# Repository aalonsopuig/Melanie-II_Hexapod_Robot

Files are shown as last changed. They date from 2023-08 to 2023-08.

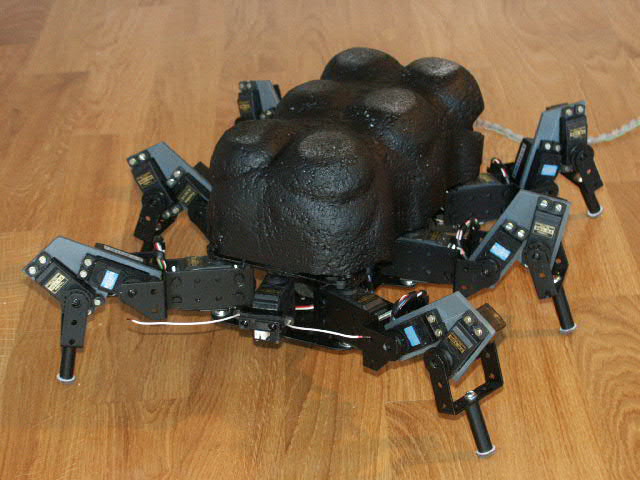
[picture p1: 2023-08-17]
Media/PICT0081.JPG

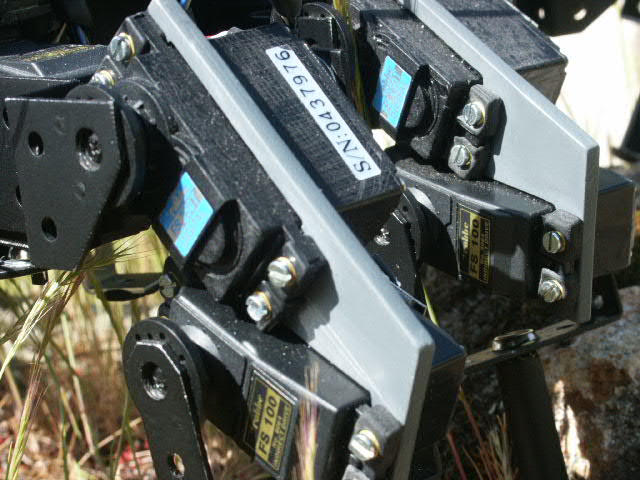
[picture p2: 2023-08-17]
Media/PICT0013.JPG

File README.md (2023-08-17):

<html>

<head>
<meta http-equiv="Content-Language" content="es">
<meta name="GENERATOR" content="Microsoft FrontPage 4.0">
<meta name="ProgId" content="FrontPage.Editor.Document">
</head>

<font size="4"><b><i>Melanie-II&nbsp;</i></b></font>
      <p>By Alejandro Alonso Puig<br>
      April 2004<br>
 
<hr>
<i>Melanie-II was developed by Alejandro Alonso on April 2004. This robot won the Hispabot 2004 National Robotics Contest at Spain.</i><br />
<i><br /></i>
<br />


<br />
Melanie is an hexapod robot of 3 degrees of freedom by leg, that by the novel design of legs it has, can transport several kilograms on its body without electrical power overload.&nbsp;The tests in laboratory have shown their capacity to rise and to walk at least with 4'5kg of additional charge, twice its own weight. See Video with <a href="https://youtu.be/sboOQ4rsUIg">Melanie-II carrying 4 bricks of milk</a><br />
<br />
<div>
<div style="text-align: center;">
<i><br /></i></div>
The version II that is showed in this technical report is an evolution of <b><u><a href="http://automacomp.blogspot.com.es/2004/03/melanie-v10-robust-hexapod-robot-of-3.html">Melanie-I</a></u></b>, to which some interesting capacities have been added, like the direct programming, the generation of movements by<br />
displacement of waves combined with inverse kinematics, or the capacity to walk on rough terrain. See Video with <a href="https://youtu.be/cWKl-8FBR9Y">Melanie-II walking over rough terrain</a><br />
<br />
There is a version III with superior capacities. Complete information could be obtained here: <b><u><a href="http://automacomp.blogspot.com.es/2004/09/melanie-iii-robust-hexapod-robot-of-3.html">Melanie-III</a></u></b><br />
<div>
<br /></div>
Some basic characteristics that define Melanie-II are the following:<br />
<br />
<i><u>Mechanics</u></i><br />
<ul>
<li>Size (cm): 33 x 31 x 20</li>
<li>Weight: 2.1 Kg</li>
<li>Structure of PVC and Aluminum</li>
<li>6 Legs. 3 degrees of freedom by leg.</li>
<li>Design of legs optimized to diminish consumption and to maximize power&nbsp;</li>
<li>Driven by radio control servos (Twelve of 3kgcm and six of 5kgcm)</li>
</ul>
<i><u>Electronics</u></i><br />
<ul>
<li>Servos control circuit with speed management, controlled via serial port.</li>
<li>I/O circuit, with 28 A/D conversion ports and 8 digital I/O. All chips are controlled via I2C bus. Measurement of the position of the 18 servos taking the signal of their potentiometers. Measurement of the consumption of energy of the servos by measuring the voltage drop in resistances of ½ ohm.&nbsp;</li>
<li>Battery of 6v NiMH 3300mAh for the servos</li>
<li>Battery of 9v NiCd for the control electronics</li>
<li>Distance measurement infrared sensor located at the front and able to be oriented</li>
</ul>
<i><u>Programming</u></i><br />
<ul>
<li>Control program in PC developed in Visual C++ 6.0</li>
<li>Movement sequence recording via direct programming</li>
<li>Movements generation by displacement of three simultaneous waves and use of inverse kinematics algorithms.</li>
<li>Detection of obstacles on the ground by detection of the variation in the current consumption and adaptation of the legs and trajectories to resolve it.</li>
</ul>
<br />
In this work there will be mention to all the mechanical, electronic and programming aspects, as well as conclusions of the experience.<br />
<br>
<br>
More information: <br>
<ul>
  <li><p align="justify"><a href="Documentation\melanie-II_doc_en.pdf">Technical documentation</a></li>
  <li><p align="justify"><a href="Melanie-II_Program">Program</a></li>
  <li><p align="justify"><a href="Media">Pictures</a></li>
  <li><p align="justify"><a href="https://github.com/aalonsopuig/Melanie-I_Hexapod_Robot.git">Repository of Melanie-I</a></li>
  <li><p align="justify"><a href="https://github.com/aalonsopuig/Melanie-III_Hexapod_Robot.git">Repository of Melanie-III</a></li>
</ul>

</body>

</html>

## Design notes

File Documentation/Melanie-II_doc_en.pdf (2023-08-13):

mundobot.com | Alejandro Alonso-Puig

# Melanie v2.0 Robust hexapod robot of 3 dof¹ /leg for rough terrain

Alejandro Alonso-Puig – mundobot.com April 2004

1
DOF: Degrees of Freedom

## Introduction

Melanie is an hexapod robot of 3 degrees of freedom by leg, that by the novel design of legs which it has, can transport several kilograms on its body without excessive power overload.

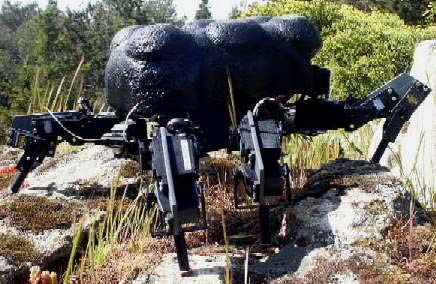
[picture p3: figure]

Some basic characteristics that define Melanie v2.0 are the following ones:

Mechanics

- Size (cm): 33 x 31 x 20
- Weight: 2.1 Kg
- Structure of PVC and Aluminum
- 6 Legs. 3 degrees of freedom by leg.
- Design of legs optimized to diminish consumption and to maximize power
- Driven by radio control servos (Twelve of 3kgcm and six of 5kgcm)

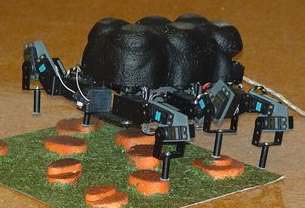
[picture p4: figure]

Electronics

- Servos | control | circuit | with | speed
management, controlled via serial port.
- I/O circuit, with 28 A/D conversion ports and 8 digital I/O. All chips are controlled via I² C
bus. Measurement of the position of the 18
servos | taking | the | signal | of their
potentiometers. | Measurement | of | the

consumption of energy of the servos by measuring the voltage drop in resistances of ½ ohm.
- Battery of 6v NiMH 3300mAh for the servos
- Battery of 9v NiCd for the control electronics
- Distance measurement infrared sensor located at the front and able to be oriented

Programming

- Control program in PC developed in Visual C++ 6.0
- Movement sequence recording via direct programming
- Movements generation by displacement of three simultaneous waves and use of inverse kinematics algorithms.
- Detection of obstacles on the ground by detection of the variation in the current consumption and adaptation of the legs and trajectories to resolve it.

In this work there will be mention to all the mechanical, electronic and programming aspects, as well as conclusions of the experience.

## Mechanics

Body

The trunk of Melanie is formed by a central chassis made out of two aluminum preperforated plates of 2mm, on which they are attached the six legs it has.

It has been procured the maximum symmetry possible in the body so that the center of gravity is the most centered possible and thus improves the physical behavior of the robot and distributes in a suitable way the effort throughout the legs.

The robot has been equipped with a shell of light porespan to protect the electronics and give it a more “animal” aspect.

Legs

The legs are made of aluminum of 2 mm and PVC of 4 mm. The structure of them differs from the habitual distribution of joints of the leg of an insect.

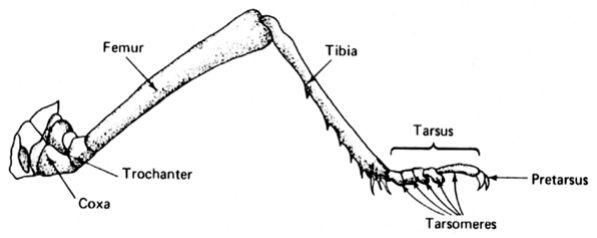
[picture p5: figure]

The Coxo-trochanter and trochanter-femur joints of an insect practically are fused, and they take care of the movements of femur in the space. The femur- tibia joint takes care of the movements of the tibia in the plane vertical to the ground.

The mechanical implementation of this structure usually is limited to three degrees of freedom and traditionally it implies the necessity to have an important torque in the servos due to the length of the femur. As longer it is, greater torque will be necessary in the motors. In addition, once carried out the elevation of the body, a great amount of energy is usually needed to maintain it in this position.

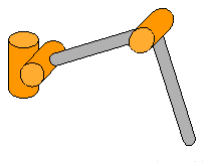
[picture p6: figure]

Traditional legs structure

The structure of legs of Melanie varies of the common structure shown in the above figure, modifying the position of the joints as it is shown the following figure:

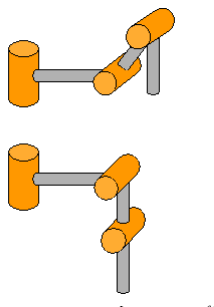
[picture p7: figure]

Legs structure of Melanie

With this structure two important advantages are obtained with respect to the traditional one shown previously:

1. Once elevated the body they are aligned the joints that allow the displacement in the vertical plane of the legs, which implies a drastic reduction of the energy consumption due to a reduction on the load in the motors of these joints. The final implementation has shown that in raised state the provision of energy to the motors can be cut and the robot will remain elevated, even with an additional charge (test with 1kg on its body). It is for that reason that will also be able to carry important additional charges in this position.
2. When moving the joint of the trochanter-femur zone to the femur-tibia zone, the mass center of the motors is moved towards the tibia, which releases of weight the trunk increasing the capacity to support a greater weight over it. The tests made have allowed verifying that each leg is able to elevate a weight of 800 grams in addition to the own weight of the leg. Reason why with 6 legs a trunk of 4,800 grams would be elevated. In the test bench the robot, of 2,1kg has risen with an additional charge of 4Kg.

The servo used are of 3Kgcm of torque for coxa and tibia joint and 5kgcm for the intermediate joint.

All the servos used have been mounted with false back shaft to assure a suitable attachment that avoids the torsions on the servo shaft.

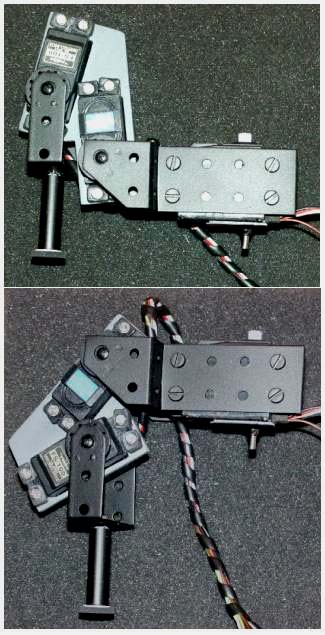
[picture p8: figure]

Leg structure of Melanie

## Electronics

Melanie v2.0 is based fundamentally on two cards: A commercial circuit of management of servos controlled by serial port RS232C of low cost and a I/O card with 28 A/D conversion ports and 8 digital ports.

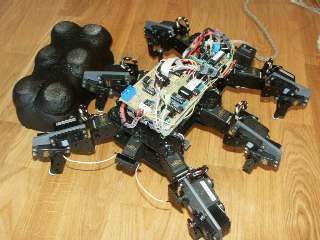
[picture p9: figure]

Servos control card

Card MSCC20 from Oricom Technologies (www.oricomtech.com) allows the control of up to 20 servos and in addition it allows to control the speed of each servo independently with just a single command.

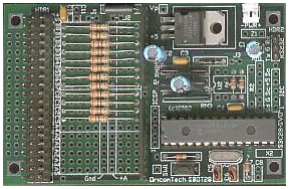
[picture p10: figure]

For additional information on this card it could be accessed its Internet web page, in which it will be found explanation of the usable Set of commands:
http://www.oricomtech.com/svo-cc.htm

The card is fed by a battery of 9v, being the servos fed by a battery of 6v NiMH 3.300 mAh

The card is connected via three wires cable to a PC serial port (RS232C) from which the control commands are sent.

I/O card

I/O Card is compound basically of 7 Chips PCF8591 (quadruple A/D of 8 bits controlled by I

2
C) and a chip PCF8574 (port expander of 8 bits by I²
C)

The 28 A/D channels are used for the measurement of the position of the 18 servos taking the signal from their potentiometers, for the measurement of the energy consumption of the 5Kgcm servos, measuring the fall of tension in resistance of ½ ohm and for the measurement of batteries voltage. As reference voltage it has been used 2,4v for the chips which measure the position of the servos and 1,4v for the chips which measure the consumption of the servos and the voltage of the batteries. For more details see the circuit diagram that is in the following figure.

Of the 8 digital channels only it is used one (channel 4). This channel activates the driver TC4425 that feeds a relay. This relay is used to cut the tension that goes to the 5Kgcm servos. This is used to reset servos since they are digital servos, that even maintain the position if we cut PWM signal. Causing a short fall of the tension in servo after stopping PWM signal they remain deactivated. Normal servos do not require this current cut as it is enough to stop the PWM signal in order to stop them. This deactivation is used for two aims: To deactivate by program the servos after a period of operation and to deactivate selectively servos to be able to move them manually and thus to make the direct programming.

Since I/O card is controlled by I²
C bus, it is used
an interface card between the robot and the external computer from which it is controlled. This card is the Velleman K8000. It is a commercial interface from parallel port to bus

I

2
C. Additional information could be obtained at: www.velleman.be or consulting the work of the author on the compatible KI²
C card of low cost in
http://www.mundobot.com/tecnica/ki2c/spki2c.htm

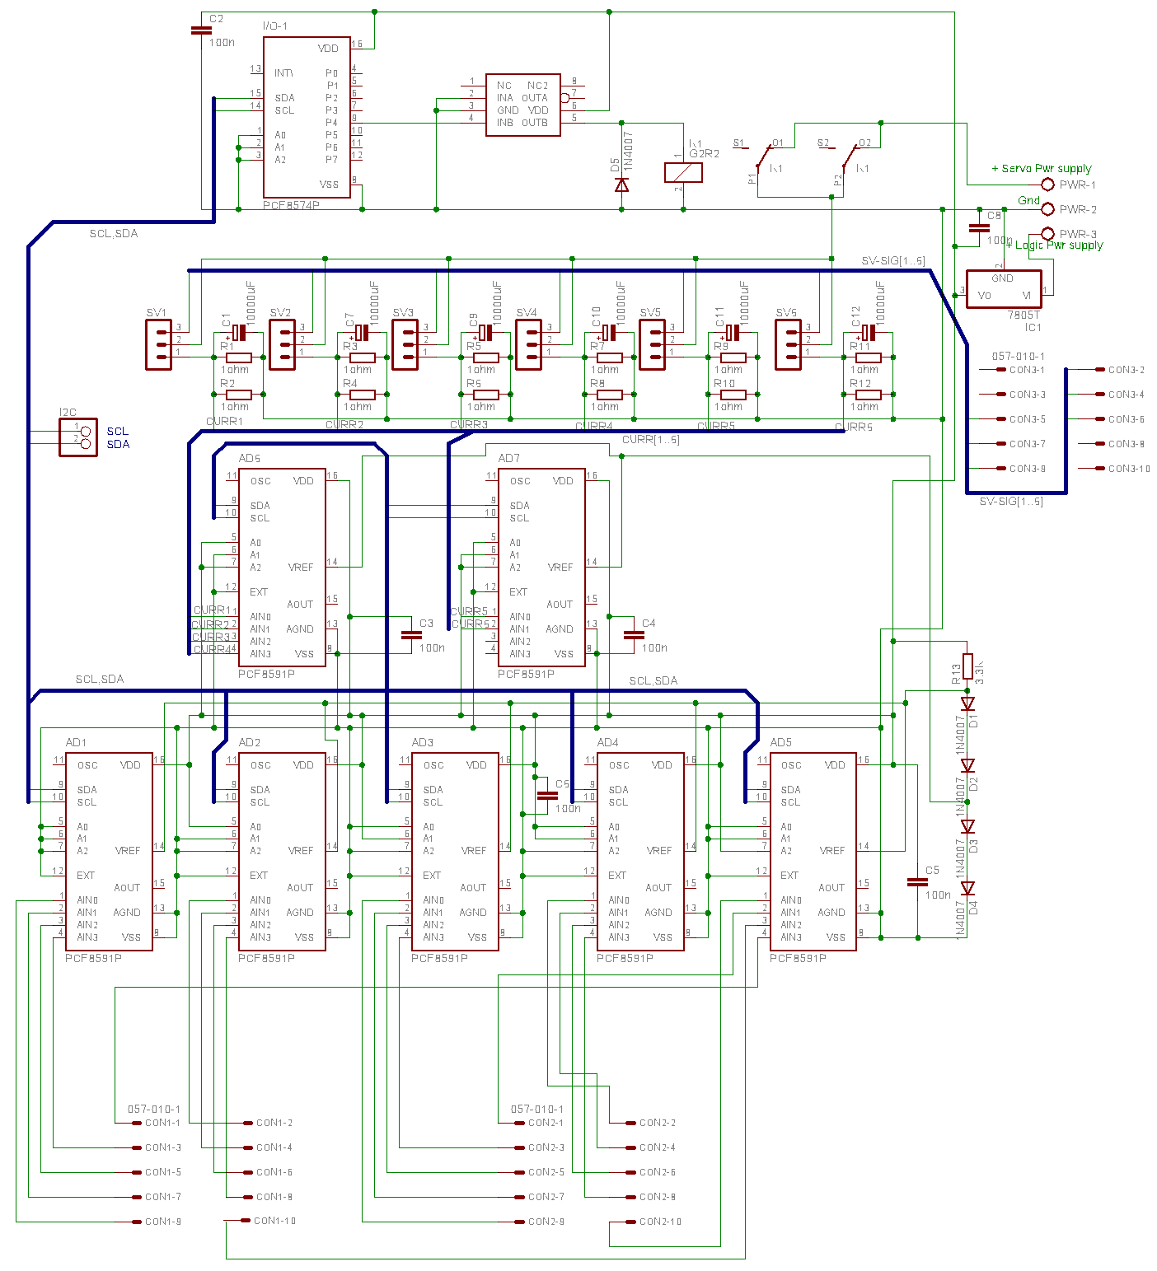
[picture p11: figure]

Following it is the relation of elements connected to connectors CON1, CON2 y CON3:

CON1-1 | Nothing | CON1-2 | Potentiometer Servo 12
CON1-3 | Potentiometer Servo 11 | CON1-4 | Potentiometer Servo 13
CON1-5 | Potentiometer Servo 6 | CON1-6 | Potentiometer Servo 5
CON1-7 | Potentiometer Servo 4 | CON1-8 | Potentiometer Servo 3
CON1-9 | Potentiometer
Servo 2 | CON1-10 | Potentiometer Servo 1
CON2-1 | Potentiometer Servo 14 | CON2-2 | Potentiometer Servo 15
CON2-3 | Potentiometer Servo 16 | CON2-4 | Potentiometer Servo 7
CON2-5 | Potentiometer Servo 8 | CON2-6 | Potentiometer Servo 9
CON2-7 | Potentiometer Servo 18 | CON2-8 | Potentiometer Servo 17
CON2-9 | Potentiometer Servo 19 | CON2-10 | Nothing

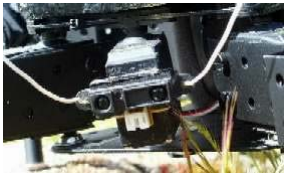
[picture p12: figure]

CON3-1 | Nothing | CON3-2 | PWM signal Servo 2
CON3-3 | Nothing | CON3-4 | PWM signal Servo 12
CON3-5 | PWM signal Servo 5 | CON3-6 | PWM signal Servo 15
CON3-7 | PWM signal Servo 8 | CON3-8 | Nothing
CON3-9 | PWM signal Servo 18 | CON3-10 | Nothing

On the other hand, to the connectors SV1,..SV6 they are connected the following digital servos (It would work the same with normal analogical servos):

SV1 | Servo 2 | SV2 | Servo 12
SV3 | Servo 15 | SV4 | Servo 18
SV5 | Servo 8 | SV6 | Servo 5

I

2
C addresses of the different chips are hardware set to the following decimal values:
AD1 | 144 | AD2 | 146
AD3 | 148 | AD4 | 150
AD5 | 152 | AD6 | 154
AD7 | 156 | I/O-1 | 64

Sensors

The robot has a GP2D12 infrared distance sensor in the frontal part, but in the present version it is not used.

## Software

For the control of the robot it has been developed the application "Melanie v2.0" in Visual C++ 6.0. This application is located in an external computer (Pentium II - 233Mhz, 64Mb ram, Windows 98). It sends the suitable commands to the servo control card of the robot via serial port and to the I/O control card by bus I²
C. This
control by bus I²
C is performed via the K8000 or KI²
C interface card connected to the parallel port that has been mentioned in the section of Electronics. The control of this card is carried out by specific libraries. For more details, see the work of the author in which its use is specified
widely: http://mundobot.com/tecnica/ecoi2c/specoi2c.htm

Use of the application

The interface with the user consists basically of the following dialogue box:

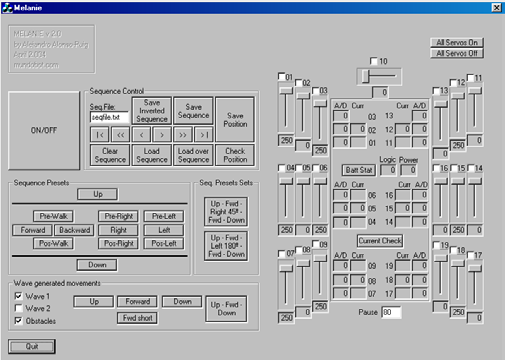
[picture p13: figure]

The dialogue box shows a series of controls that allow controlling the robot in a manual way and generating sequences of movements that can be recorded and later reproduced.

In order to activate the robot the button ON/OFF should be pressed, that will activate the legs maintaining them where they are.

Recording/Reproduction of sequences

The recording of sequences can be carried out by two ways:

- Moving the servos by means of sliding controls and recording the positions.
- Moving manually the legs and recording the positions by means of direct programming

Sliding controls

The right part shows the positioning values of the servos. Moving each slider control a servo will move.

A sequence could be recorded by positioning servos as desired so that the robot has a determined position, establishing a value of pause (field underneath the scheme of the robot), that will determine the time that should happen between the position that previously it had and the new one requested. Depending on this value, that will come measured in second hundredth, a greater or smaller speed will be applied to the servos.

Once selected position and pause, would press the button "Save Position" of the "Sequence Control" area, that will store the new position in dynamic memory. Following this way it is possible to generate a complete sequence of movements. Putting a name of file in the field "Seq.File" and pressing "Save Sequence" a file with the generated sequence will be recorded in hard disk.

Direct programming

In order to carry out this programming it would be necessary to deactivate the desired servos to be able to move them manually. This is carried out unmarking check-box of the wished servos in the right part of the screen. After this they could be moved manually to the wished position.

Once selected position and pause, we should press the button "Check Position", that will verify the position of legs servos and then "Save Position" of the area "Sequence Control", that will store the new position in dynamic memory. In this way we could store a complete sequence of movements. Putting a name of file in the field "Seq.File" and pressing "Save Sequence" a file with the generated sequence will be recorded in hard disk.

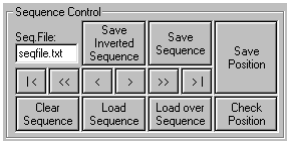
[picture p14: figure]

The other controls of the area "Sequence Control" carry out the following functions:

- Save Inverted Sequence: It records the sequence but in inverse way. Very useful when a movement is identical to another existing one but in the inverse way, like for example walking forwards and backwards
- Clear Sequence: Deletes the sequence that is in memory
- Load Sequence: Load in memory a prerecorded sequence. The name of the sequence file should be specified in the field "Seq.File"
- Load over Sequence: Load in memory a sequence from the present position of the pointer, that is to say, if we have a sequence in memory and we move to its end with the buttons we will explain later, we can press "Load Over Sequence" to load a sequence on the existing one in memory from the present position. This way we could connect sequences.
- "|<" Allows to be placed at the beginning of the existing sequence in memory
- ">|" Allows to be placed at the end of the sequence
- ">" Allows to advance a position in the sequence loaded in memory. This allows going step by step in the sequence for debugging.
- "<" inverse case of previous one
- ">>" Allows to reproduce the sequence from the present position to the end without interruption
- "<<" Just as the previous one but in inverse way.

With the previous controls it is possible to debug positions with advancing step by step, to correct the position wished with the slider controls and to press "Save Position".

It is necessary to consider that pressing this button overwrites the position of all servos in the present place of the sequence and the sequence pointer moves to the following position being prepared to overwrite it. If it is only wanted to overwrite a position, it will be done as indicated and then "<" and ">" should be clicked so the robot is forced to be placed according to the following position.

There is a series of prerecorded basic sequences that will allow moving the robot. These sequences are grouped under the set "Sequence Presets". They allow raising the robot, making it walk, turn...

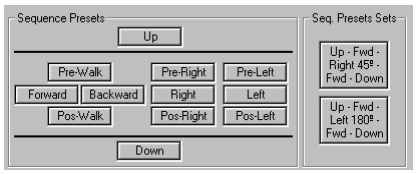
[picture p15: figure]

Additionally there is a group of sets of sequences prerecorded under the set "Sequence Preset Sets" that allow to execute several simple sequences of the indicated previously, to carry out a concrete task, demonstration, etc, like rising, walking, turning around and lying down.

Movements by displacement of waves over rough terrain

There is another area at the screen (wave generated movements) that allows controlling the robot not by playing recorded sequences, but by means of a system called waves displacement. The robot generate the movements based on triple overlapped waves.

The program is prepared for two kind of waves: Wave 1 and Wave 2. The first one makes the robot walk in the typical tripod mode, it means, walking with alternate triangles of legs so they are always three legs on the floor.

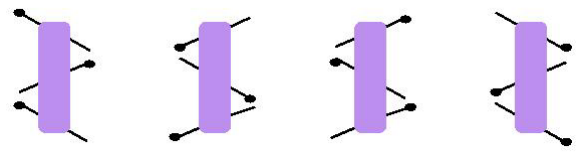
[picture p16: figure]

The second mode move the legs in a way so there are always five legs on the floor.

Also it is possible to make the robot sensible or not to obstacles on the floor by using the checkbox “Obstacles”. In case this mode is used, the robot will be able to walk in rough terrain, detecting obstacles like stones, walking over them while maintaining the body horizontal to the floor.

Application design

The application has been generated in Visual C++
6.0. It uses a library developed by P.J. Naughter for the control of the serial port with which the robot will communicate.

For more information on using the mentioned library the work of the existing author can be consulted in the direction:

http://www.codeproject.com/system/cserialport.asp

Additionally it uses a library for the control of the parallel-I²
C interface.

For more information on this library the following report could be reviewed:
http://mundobot.com/tecnica/ki2c/spki2c.htm

The interface with the user consists basically of a dialogue box associated to a CMelanieDlg class within which there are all the functions and variables used for the control of the robot.

The source code of the application contains numerous commentaries and can be acceded in the direction:
http://mundobot.com/projects/melanie/melanieprg.zip

In any case next we will explain the general structure of the application.

Recording/Reproduction of sequences

As it was explained previously, it is possible to store sequences of movements. In order to carry out this, pointers to structures stored in dynamic memory are used.

struct stPosition
{
unsigned char | cServoPos[21],
| cPause;
struct stPosition | *nextpos,
| *prevpos;
};

In each element of this structure we can store a complete position, that includes the 20 positions of servos and delay that must have between the previous position and this one. Additionally they are stored pointers both to previous and next elements to have a linked list in which we could move freely forward and backward.

The storage of the mentioned structure is performed when pressing the button “Save Position” which calls the function “OnSavepos()”. This function takes the servos position values and store them in the structure.

If direct programming is being performed, before pressing the button “Save Position” it is needed to press the button “Check Position” which will call the function “OnAD()” and this to “ChkPos(unsigned
char cPos[20],unsigned char cAD[20])” which takes the
servos position values by reading the analog values of the servos internal potentiometers. This value is converted to a byte value that if sent with the positioning command to the servo control card would move the servo to the position it is right now. To get this, the program have a table (byte bCal[21][4]) which stores four values for each servo that correspond to two different positions of the servos (a couple of values for each of the two positions). Each couple have interrelated values. The first one is the value sent to the servo control card to move the servo to that position. The second one is the analog measurement of the position. Having this for two different positions A and B (see figure), it is possible to obtain the rest of the values of the line that cross both points. Lets see this with an example:

Servo number 1 has been positioned with the slider controls to the value 20 (showed in the dialog box), then potentiometer value has been measured (A/D conversion). The value obtained has been 59. The same thing has been done locating the servo to position 198 obtaining the A/D value 195. As there is a linear relation between the positioning value and the A/D value,

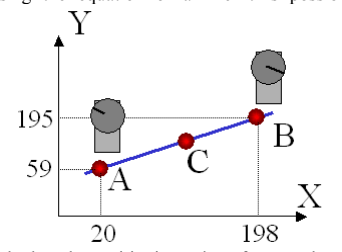
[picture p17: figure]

calculate the positioning value of a servo based on the A/D value measured. Then, if for example the value read from the potentiometer is, lets say 90, we will obtain the positioning value as showed here:

using the equation of a line it is possible to

osition = X axis

o points of the line = (20,59) y (198,195)

b = m(y-a) {Cartesian equation of a line}

sing the points: (x=20 , y=59, a=198, b=195)

-195= m(20 - 198)

= (59-195)/(20 - 198)

en :

-195 = m(x - 198) = (59-195)/(20-198)*(x-198)

D-195 = (59-195)/(20-198)*(POS-198)

OS = 198+(AD-195)/((59-195)/(20-198))

herefore, for AD=90, POS=60’6

has been taken therefore the values of A y B

he existing sequence in memory can be saved to

nly could be reproduced sequences that are

he execution of each step of the sequence is

P
AD = Y axis

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
empirically for all servos and charged them in the matrix bCal as part of the program code. In case of changing the servos, it would be necessary to calibrate them and to update the values of this matrix again.

T
a file using the function "OnSaveseq()"and load a
file | in | memory | using | the | function
"LoadSequence(CString FileName)" that is called from other several functions.

O
loaded in memory, so the buttons of prerecorded sequences simply will call to functions that load in memory a prerecorded sequence and executes it.

T
carried | out | by | calling | the | function
"SetGlobalPos()", that will move servo and slider controls according to the values of the present pointer.

The delay (Pause) as it was mentioned, will indicate the time that must pass between a position and another one. So that died moments do not exist, function " cSpeed(unsigned char cServo)" will calculate the speed that should apply to each servo depending on the mentioned pause and the run to carry out. It is based on specifications from the manufacturer of the servo control card that indicates that the speed parameter has to be an integer value between 1 and 255 that can be calculated according to the following formula:

T

Pos Pos V 8( | 1− | 0) =

where T is the time in second hundredth that is desired to take the servo to go from a position to another one, being Pos1 the position of greater value and Pos0 the position of lower value. The values of Pos1 and Pos0, according to specifications of the manufacturer of the servo control card, have to be integer values between 0 and 250.

The commands for the servo control card are
mainly | sent | by | using | the | function
"SendCommand(CString sCommand)".

Although the servo control card admits great amount of commands, we will use only the following ones:

- SO: It turn all servos on
- SF: turn all servos off
- SX1F9D: Set excursion limits of all servos to 496µsg and 2.512µsg
- SEss: It activates the generation of pulses for servo "ss", value that should be in hexadecimal 00 - 13h (19d).
- Mssddvv: It moves servo "ss" (hexadecimal value) to the 8 bits position "dd" (hexadecimal value between 00 and FAh [ 250d ]) at speed "vv" (hexadecimal value between 1 and FFh [ 255d ])

For more information on the commands available and their use, go to the documentation of the manufacturer:
http://www.oricomtech.com/sub2/msc2-cmd.htm

Movement by displacement of waves

As told before, the robot can move generating himself the positions instead of using prerecorded positions. The way in which it makes this is by using three waves whose values will vary in the time and will define the values of coordinates (x, y, z) in the space for the end of each leg.

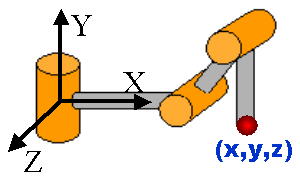
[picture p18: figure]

Having these values, a geometric algorithm of inverse kinematics will be used and the value of positioning of each servo will be obtained so that the end of the leg is placed in the indicated coordinates.

Inverse Kinematics

The program do all the inverse kinematics calculations needed by using the following function:

Int InvKinematic(double value[2][3], double result[3])

This function return 0 if it has not happened any error in the calculation (for example it could occur that the given coordinate is outside the reachable space of the leg).

The input data for the
function | will | be
loaded in the matrix
value[2][3] so that the
first row of data will
contain the lengths in

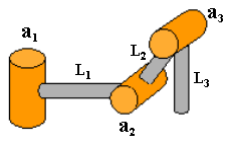
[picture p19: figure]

millimeters of the three parts of the leg (L1, L2, L3) and the second row will contain the coordinates (x, y, z) that is desired that it has the end of the leg respect to his origin of reference. As result the function loads in the matrix result[3] the values in degrees of the angles the joints should have (a1, a2, a3)

The algorithm used for the calculation of the inverse kinematics use the geometric method.

Later the values of angles (in degrees) of each servo can be converted to positioning values accepted by the servo control card by using the
function unsigned char cConvDegToPos(char cServo,
double Deg), where cServo is the number of the servo we are referring to and Deg is the value in degrees we desire this joint to have. The value returned by the function is the value to be sent to the servo control card.

In order to obtain this, values of calibration for each servo are used that have been taken empirically and are loaded at the beginning
of the program in matrix cPosConv[20][2].

The first index indicates the servo and the second index indicates a position of 0 degrees and one of 45 degrees. For example, for leg 1 the following values are loaded:

cPosConv[ 1][0]=203; | cPosConv[ 1][1]=140;
cPosConv[ 2][0]= 77; | cPosConv[ 2][1]=136;
cPosConv[ 3][0]=103; | cPosConv[ 3][1]=160;

The first row includes the values for servo 1. 203 is the value that requires the servo control card for positioning the servo so that the angle of the joint is 0 degrees and 140 is the value that requires the servo control card for positioning the servo so that the angle of the joint is 45 degrees.

With these values and, given to the linear relation between value of positioning and angle in degrees of the joint, we can always obtain the value of positioning of the servo based on the value of the angle of the joint by using the equation of a line.

It exists an inverse function to this called
double cConvPosToDeg(char cServo, unsigned char cPos)

Direct Kinematics

The program also carries out in some cases direct kinematics calculations. For it it uses the function:

int FwdKinematic (double value[2][3], double result[3])

This function returns 0 if it has not happened any error in the calculation.

The used algorithm is also of geometric type.

The input data for the
function | will | be
loaded in the matrix
value[2][3] so the first
row of data will
contain the lengths in

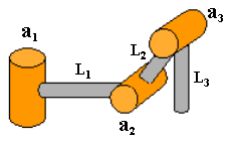
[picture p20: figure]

millimeters of the three parts of the leg (L1, L2, L3) and the second row will contain the angles in degrees of the joints (a1, a2, a3). As result the function will load in the matrix result[3] the values of the coordinates (x, y, z) that the end of the leg will have respect to its origin of reference.

Generation of waves

As told before, they are three waves those that define the coordinates that each leg will have at every moment.

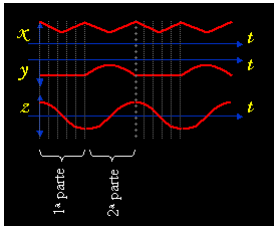
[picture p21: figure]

Coordinate X is calculated by means of a triangular wave, the coordinate Y by means of a half-wave and coordinate Z by means of a complete sine wave. The frequency of the triangular wave has to be double of the other two so that the leg moves suitably.

Varying the phase angle between the waves of the different legs and the relation between the length from the first (1ª Parte) and second part (2ª Parte)

of the cycle of the wave we will obtained different "gaits".

The first part of the cycle corresponds to the moment at which the end of the leg is touching the ground and moving backwards (body advancing), whereas the second part of the cycle corresponds to the elevation and displacement ahead in arc of the leg (positioning for a new step). Thus for example in the previous figure, the first and second part of the cycle is of the same length (in time), so it will take the same time in moving backwards the leg that in positioning it again ahead. If we used this type of waves
in all the legs, but we apply a phase angle of 180 degrees to three of the legs, we will obtain a tripod "gait", so the body always will be supported by three legs.

If for example we use waves of the previous type, but with the 2nd part of the cycle of a length 1/5 of the one of the 1st part the leg will rise and place ahead in a determined time, whereas it will move backwards 5 times slower.

If we combine this situation with a phase angle of 36º (180/5) between the waves of the different legs we obtain a "gait" according to which always there will be 5 legs on the ground and one in the air, but the body will be moving ahead with a continuous speed.

This is not accidental. If we wish that the body moves at continuous speed, it always has to have a sufficient number of legs in contact with the ground being moved backwards, not being anyone stopped. If we want that always there are 5 legs in contact with the ground, it will be necessary to raise the legs one by one, so that the 5 legs should have enough time to rise and be placed at the front in consecutive way in the time that the sixth leg moves backwards. So the time for the elevation and displacement of a leg in the air to the front will have to be 1/5 of the time that takes in moving the leg backwards. This is indeed the length in time of 2nd part of the cycle. On the other hand, as it is desired that only one leg is in the air at each moment (5 legs in the ground), the waves of the legs will have to be moved 1/5 of

180º, since 180º is the point in which the wave change from the 1st to the 2nd part of the cycle.

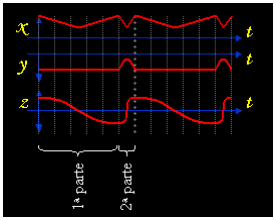
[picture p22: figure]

It is important in this point to stand out that the waves used are those indicated at the beginning of this section, so triangular, half-wave and complete sine wave and that the variation of the length in time of 1st or 2nd part of the cycle is just a kind of "stretching" of the time and therefore the values in degrees also "stretch". Lets see what we are talking about for the previous case of the sine wave (Cosenoidal) that generates the value of coordinate Z:

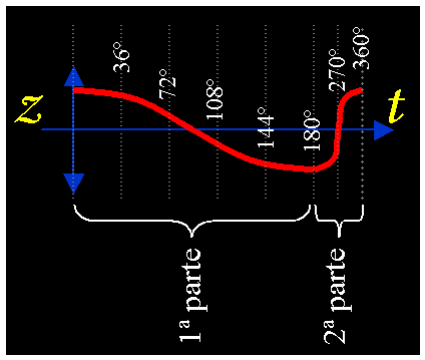
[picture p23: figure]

In the program it is the function void OnWaveFwd() that will make the robot walk forward according to the method of displacement of waves explained.

Following the same method of displacement of waves the MoveLeg function has been generated, that moves the end of one or several legs from a point in the space to another one, either with a straight line displacement between both points or making an arched movement of rise, displacement and go down.

It must be remembered that the coordinates handled for each leg are always relative to the point of coordinates of each leg, as showed in the following figure:

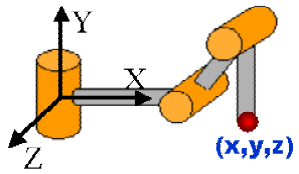
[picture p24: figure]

Obstacles detection

The program is prepared for the detection of obstacles on the ground and to adapt the "gait" to allow the robot to walk over these obstacles.

The way it is done is by measuring the consumption of current by the servos at the moment the leg is going down to put its end on the ground.

The measurement of the current consumption is done by the function void ChkCurr() that sends the needed commands to carry out the reading of A/D converters by bus I²
C and load in the
Current[6] matrix the values of measurement of current for the 6 servos that more force have to make to support the body.

If the consumption measurement is over a given threshold, the leg stops, its position is obtained and the length of the second part of the cycle of the waves of this leg is modified temporarily. Also a small phase angle is added to assure that they move with coordination with the rest of legs. The values of phase and length of the second part of the cycle of this leg return to its normal values in the following cycle, with no disruption in the continuity of the waves during the transition.

## Bibliography and interesting links

Agricultural Entomology. Daniel G. Pesante Armstrong. Chapter 7: http://www.uprm.edu/wciag/anscience/dpesante/4008/cap-7.PDF Puchobot. Quadruped Robot. Andrés Prieto Moreno: http://www.iearobotics.com/personal/andres/proyectos/pucho/pucho.html Cube Reloaded. Worm robot. Juan González: http://www.iearobotics.com/personal/juan/doctorado/cube-reloaded/
Direct & inverse kinematics course (Univ.Guadalajara-Mexico):: http://proton.ucting.udg.mx/materias/robotica/r166/r78/r78.htm
Legs. General design considerations: http://www.frasco.demon.co.uk/rodney/mechan/design.htm The Walking Machines Catalogue: http://www.walking-machines.org/
Silo4. Quadruped Robot developed by CSIC. Spain: http://www.iai.csic.es/users/silo4/
An introduction to robot kinematics: http://www.generalrobotics.org/ppp/Kinematics_final.ppt MSCC20. credit card-sized control computers for driving up to 20 R/C servos. Oricom Technologies: http://www.oricomtech.com/svo-cc.htm
CSerialPort v1.03 - Serial Port Wrapper. PJ Naugter: http://www.codeproject.com/system/cserialport.asp

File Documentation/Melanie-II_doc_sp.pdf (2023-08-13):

mundobot.com | Alejandro Alonso Puig

# Melanie v2.0 Robot hexápodo robusto de 3 dof¹ /pata para terrenos abruptos

Alejandro Alonso Puig – mundobot.com Abril 2004

1
DOF: Degrees of Freedom = Grados de Libertad

## Introducción

Melanie es un robot hexápodo de 3 grados de libertad por pata, que por el novedoso diseño de patas de que dispone, puede transportar varios kilos sobre su cuerpo sin excesiva sobrecarga energética.

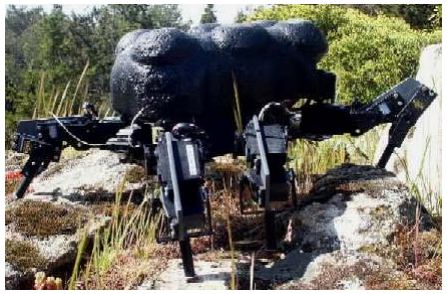
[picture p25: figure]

Algunas características básicas que definen a Melanie v 2.0 son las siguientes:

Mecánica

- Medidas (cm): 33 x 31 x 20
- Peso: 2.1 Kg
- Estructura de PVC y Aluminio
- 6 Patas. 3 grados de libertad por pata.
- Diseño de patas optimizado para minimizar consumo y maximizar potencia
- Accionamiento | mediante | servos | de
radiocontrol (Doce de 3kgcm y seis de 5kgcm)


Electrónica

- Circuito de control de servos con gestión de velocidad, controlado por puerto serie.
- Circuito I/O, con 28 puertos de conversión A/D y 8 entradas/salidas digitales. Todos los chips son controlados por bus I²
C. Medición
de la posición de los 18 servos tomando la señal de sus potenciómetros. Medición del consumo de energía de los servos midiendo la caída de tensión en resistencias de ½ ohm.
- Batería de 6v NiMH 3300mAh para la alimentación de los servos
- Batería de 9v NiCd para la alimentación de la electrónica de control
- Sensor de medición de distancia por infrarrojos delantero orientable

Programación

- Programa de control en PC desarrollado en Visual C++ 6.0
- Grabación de secuencias de movimiento por programación gestual
- Generación | de | movimientos | por
desplazamiento de tres ondas simultáneas y aplicación de algoritmos de cinemática inversa
- Detección de obstáculos en el suelo por variación en el consumo de corriente y adaptación de las patas y trayectorias para solventar los mismos.

En este trabajo se hará mención a todos los
aspectos | mecánicos, | electrónicos | y | de
programación, así como conclusiones de la experiencia.

## Mecánica

Cuerpo

El tronco de Melanie está formado por un chasis central consistente en dos planchas de aluminio preperforado de 2mm sobre el que se acoplan las seis patas de que dispone.

Se ha procurado la máxima simetría posible en el cuerpo para que el centro de gravedad quede lo más centrado posible en el mismo y así mejorar el comportamiento físico del robot y distribuir de forma adecuada el esfuerzo de las patas.

Se ha dotado al robot de un caparazón de porespan ligero para proteger la electrónica y dotarle de una imagen más “animal”.

Patas

Las patas se han construido en aluminio de 2 mm y PVC de 4 mm. La estructura de las mismas difiere de la distribución de articulaciones habitual de la pata de un insecto.


Las articulaciones Coxo-trocanter y trocanter-fémur de un insecto se encuentran prácticamente fundidas entre si y se ocupan de los movimientos del fémur en el espacio. La articulación fémur-tibia se ocupa de los movimientos de la tibia en el plano vertical al suelo.

La implementación mecánica de esta estructura suele limitarse a tres grados de libertad y tradicionalmente implica la necesidad de disponer de un par motor importante en los servos debido a la longitud del fémur. Cuanto más largo sea este, mayor par será necesario en los motores. Además, una vez efectuado el elevamiento del cuerpo, es necesaria una cuantiosa cantidad de energía para mantenerlo en dicha posición.

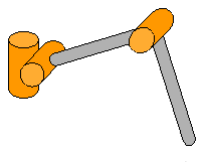
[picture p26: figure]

Estructura tradicional de patas

La estructura de patas de Melanie varía de la estructura común mostrada en la figura de arriba, modificando la posición de las articulaciones tal como se muestra en la figura siguiente:


Estructura de patas de Melanie

Con esta estructura se obtienen dos ventajas importantes respecto a la tradicional mostrada previamente:

1. Una vez levantado el cuerpo se superponen las articulaciones que permiten el desplazamiento en el plano vertical de las patas, lo que implica una drástica reducción del consumo de energía al reducir la carga en los motores de dichas articulaciones. La implementación final ha demostrado que en estado levantado puede cortarse el suministro de energía a los motores y el robot permanecerá elevado, incluso con carga adicional (test con 1kg sobre su cuerpo). Es por ello que podrá además llevar cargas adicionales importantes en esta postura.
2. Al desplazar la articulación de la zona del trocanter-fémur a la zona fémur-tibia se desplaza el peso de los motores hacia la tibia, lo que libera de peso al tronco aumentando la capacidad de soportar un peso mayor sobre el mismo. Los ensayos realizados sobre banco de pruebas han permitido comprobar que cada pata es capaz de elevar un peso de 800 gramos además del propio peso de la pata. Por lo que con 6 patas podría elevarse un tronco de 4.800 gramos. En el banco de pruebas el robot, de 2,1kg se ha levantado con una carga adicional de 4Kg.

Los servos utilizados son de 3Kgcm de par para coxa y articulación de la tibia y 5kgcm para la articulación intermedia.

Todos los servos utilizados han sido montados con falso eje posterior para asegurar un adecuado anclaje que evite las torsiones sobre el eje de los mismos.


Estructura de patas de Melanie

## Electrónica

Melanie v2.0 se basa fundamentalmente en dos tarjetas: Un circuito comercial de gestión de servos controlado por puerto serie RS232C de bajo coste y una tarjeta I/O con 28 puertos de conversión A/D y 8 entradas/salidas digitales.


Tarjeta de gestión de servos

La tarjeta MSCC20 de Oricom Technologies (www.oricomtech.com) permite el control de hasta 20 servos y además permite controlar la velocidad de cada servo de forma independiente con un solo comando.


Para información adicional sobre dicha tarjeta puede accederse a la página sobre la misma en

Internet, en la cual se puede encontrar explicación del set de comandos utilizable: http://www.oricomtech.com/mscc20.htm

La tarjeta está alimentada por una batería de 9v, estando los servos alimentados por una batería de 6v NiMH de 3.300 mAh

La tarjeta está conectada mediante un cable de tres hilos al puerto serie de un PC desde el que se envían los comandos de control.

Tarjeta I/O

La tarjeta I/O está compuesta básicamente por 7 chips PCF8591 (cuádruple A/D de 8 bits controlados por I²
C) y un chip PCF8574 (expansor de puerto de 8 bits por I²
C)

Los 28 canales A/D son utilizados para la medición de la posición de los 18 servos tomando la señal de sus potenciómetros, para la medición del consumo de energía de los servos de 5Kgcm de par, midiendo la caída de tensión en resistencias de ½ ohm y para la medición de tensión de las baterías. Como voltaje de referencia se ha utilizado 2,4v para los chips que miden la posición de los servos y 1,4v para los chips que miden el consumo de los servos y la tensión de las baterías. Para más detalles ver el plano del circuito que se muestra en la siguiente figura.

De los 8 canales digitales solo se utiliza uno de ellos como salida (canal 4). Dicho canal da señal a un driver de potencia TC4425 que alimenta un Relé. Este Relé se utiliza para cortar la tensión que va a los servos de 5Kgcm de par. Esto se utiliza para resetear dichos servos ya que son servos digitales, que mantienen la posición incluso si se corta la señal PWM de posicionamiento. Provocando una caída corta de la tensión en dichos servos tras cortar la señal PWM se quedan desactivados. Los servos normales no requieren este corte de corriente ya que al cortar la señal PWM quedan inmediatamente desactivados. Esta desactivación se utiliza para dos fines: Desactivar por programa los servos tras un periodo de funcionamiento y desactivar selectivamente servos para poder moverlos manualmente y así realizar la programación gestual.

Puesto que la tarjeta I/O está controlada por bus I

2
C, se utiliza una tarjeta interface entre el robot y el ordenador externo desde el que se controla el mismo. Esta tarjeta es la Velleman K8000. Se trata de un interfaz comercial de puerto paralelo a bus I

2
C. Se puede obtener información adicional en la página www.velleman.be o consultando el trabajo del autor sobre la tarjeta compatible de bajo coste KI²
C en http://www.mundobot.com/tecnica/ki2c/spki2c.htm


A continuación se muestra la relación de elementos conectados a los conectores CON1, CON2 y CON3:

CON1-1 | Nada | CON1-2 | Potenciómetro Servo 12
CON1-3 | Potenciómetro Servo 11 | CON1-4 | Potenciómetro Servo 13
CON1-5 | Potenciómetro Servo 6 | CON1-6 | Potenciómetro Servo 5
CON1-7 | Potenciómetro Servo 4 | CON1-8 | Potenciómetro Servo 3
CON1-9 | Potenciómetro
Servo 2 | CON1-10 | Potenciómetro Servo 1
CON2-1 | Potenciómetro
Servo 14 | CON2-2 | Potenciómetro Servo 15
CON2-3 | Potenciómetro Servo 16 | CON2-4 | Potenciómetro Servo 7
CON2-5 | Potenciómetro Servo 8 | CON2-6 | Potenciómetro Servo 9
CON2-7 | Potenciómetro Servo 18 | CON2-8 | Potenciómetro Servo 17
CON2-9 | Potenciómetro Servo 19 | CON2-10 | Nada
CON3-1 | Nada | CON3-2 | Señal PWM Servo 2
CON3-3 | Nada | CON3-4 | Señal PWM Servo 12
CON3-5 | Señal PWM Servo 5 | CON3-6 | Señal PWM Servo 15
CON3-7 | Señal PWM Servo 8 | CON3-8 | Nada
CON3-9 | Señal PWM Servo 18 | CON3-10 | Nada


Por otra parte, a los conectores SV1,..SV6 se conectan los siguientes servos, que son de tipo digital (funcionaría igual con servos analógicos normales):

SV1 | Servo 2 | SV2 | Servo 12
SV3 | Servo 15 | SV4 | Servo 18
SV5 | Servo 8 | SV6 | Servo 5

Las direcciones I²
C de los diferentes chips se han establecido por hardware a los siguientes valores:
AD1 | 144 | AD2 | 146
AD3 | 148 | AD4 | 150
AD5 | 152 | AD6 | 154
AD7 | 156 | I/O-1 | 64

Sensores

El robot posee un sensor de distancia por infrarrojos GP2D12 en la parte frontal, pero en la versión actual no es utilizado.

## Programación

Para el control del robot se ha generado la aplicación “Melanie v2.0” en Visual C++ 6.0. Dicha aplicación se encuentra localizada en un ordenador externo al robot (Pentium II – 233Mhz, 64Mb RAM, Windows 98). Se ocupa de enviar los comandos adecuados a la tarjeta de control de servos del robot vía puerto serie y controlar la tarjeta I/O por bus I²

C. Dicho control por bus I² C
se hace a través de la tarjeta interface K8000 o KI²
C conectada al puerto paralelo que se ha mencionado en el apartado de Electrónica. El control de esta tarjeta se lleva a cabo mediante el uso de unas librerías específicas. Para más
detalles | ver | el | trabajo | del | autor:
http://mundobot.com/tecnica/ecoi2c/specoi2c.htm en el que se especifica ampliamente su uso.

Utilización de la aplicación

El interface con el usuario consiste básicamente en un cuadro de diálogo como el que se muestra a continuación.


El cuadro de diálogo muestra una serie de controles que permiten manejar al robot de forma manual y generar secuencias de movimientos que
pueden | ser | grabadas | y | posteriormente
reproducidas.

Para activar el robot habrá de pulsarse en primer lugar el botón ON/OFF, que activará las patas dejándolas fijas en la posición actual.

Grabación/Reproducción de
secuencias

La grabación de secuencias puede llevarse a cabo de dos formas:

- Moviendo los servos mediante controles deslizantes y grabando las posiciones
- Moviendo manualmente las patas y grabando las posiciones mediante programación gestual

Controles deslizantes

La parte derecha muestra los valores de posicionamiento de los servos. Moviendo cada control deslizante se moverá un servo concreto.

Pueden grabarse secuencias posicionando los servos como se desee para que el robot tenga una postura determinada, estableciendo un valor de pausa (campo debajo del esquema del robot), que determinará el tiempo que habrá de pasar entre la postura que anteriormente tuviese y la nueva fijada. Dependiendo de dicho valor, que vendrá medido en centésimas de segundo, se aplicará una mayor o menor velocidad a los servos.

Una vez seleccionada postura y pausa, se pulsaría el botón “Save Position” del área “Sequence Control”, que almacenará la nueva posición en memoria dinámica. Se puede de esta manera ir guardando nuevas posiciones generando una secuencia completa de movimientos. Poniendo un nombre de fichero en el campo “Seq.File” y pulsando “Save Sequence” se grabará en disco duro un fichero con la secuencia generada.

Programación gestual

Para llevar a cabo esta programación habría que desactivar los servos que se desee para poder moverlos manualmente. Esto se lleva a cabo desmarcando los check-box de los servos deseados en la parte derecha de la pantalla. Tras esto pueden moverse manualmente hasta la posición deseada.

Una vez seleccionada postura y pausa, se pulsaría el botón “Check Position”, que verificará la posición de los servos de las patas y luego “Save Position” del área “Sequence Control”, que almacenará la nueva posición en memoria dinámica. Se puede de esta manera ir guardando nuevas posiciones generando una secuencia completa de movimientos. Poniendo un nombre de fichero en el campo “Seq.File” y pulsando “Save Sequence” se grabará en disco duro un fichero con la secuencia generada.


Los demás controles del área “Sequence Control” llevan a cabo las siguientes funciones:

- Save Inverted Sequence: Graba la secuencia pero en sentido inverso. Muy útil cuando un movimiento es idéntico a otro existente pero a la inversa, como por ejemplo andar hacia delante y hacia atrás.
- Clear Sequence: Borra la secuencia que hubiese en memoria.
- Load Sequence: Carga en memoria una secuencia pregrabada. Ha de especificarse el nombre de la misma en el campo “Seq.File”
- Load over Sequence: Carga en memoria una secuencia desde la posición actual de memoria, es decir, si tenemos una secuencia en memoria y nos colocamos al final de la misma con los botones que se explicarán a continuación, podemos pulsar “Load Over Sequence” para cargar una secuencia sobre la existente desde la posición actual. De esta manera se pueden enlazar secuencias.
- “|<” Permite colocarse al principio de la secuencia existente en memoria
- “>|” Permite colocarse al final de la secuencia.
- “>” Permite avanzar una posición en la secuencia cargada en memoria. Esto permite ir paso a paso en la secuencia para depurarla.
- “<” Caso inverso del anterior.
- “>>” Permite reproducir la secuencia desde el punto actual hasta el final sin interrupción.
- “<<” Igual que el anterior pero de forma inversa.

Con los controles anteriores es posible depurar posiciones a base de avanzar paso a paso, corregir la posición deseada con los controles deslizantes y pulsar “Save Position”.

Hay que tener en cuenta que al pulsar este botón se sobrescribe la postura de todos los servos en el lugar actual de la secuencia y el puntero de secuencia se mueve a la siguiente posición quedando preparado para sobrescribirla. Si tan solo se quiere sobrescribir una posición, se hará como se ha indicado y luego se pulsará “<” y luego “>” con lo que forzamos al robot a colocarse según la posición siguiente.

Hay una serie de secuencias básicas pregrabadas que permitirán mover el robot. Dichas secuencias se encuentran agrupadas bajo el conjunto “Sequence Presets”. Permiten levantar el robot, prepararlo para andar, girar,...


Adicionalmente hay un grupo de sets de secuencias pregrabadas bajo el conjunto “Sequence Preset Sets” que permiten ejecutar varias secuencias simples de las indicadas anteriormente para llevar a cabo una tarea concreta, demostración, etc, como levantarse, dar unos pasos, dar la vuelta y volver a tumbarse.

Movimiento por desplazamiento de ondas sobre terreno abrupto

Existe otro área en la pantalla (wave generated movements) que permite controlar el robot no mediante la reproducción de secuencias
pregrabadas, | sino | mediante | un | sistema
denominado de desplazamiento de ondas. El propio robot genera los movimientos basados en triples ondas superpuestas.

El programa está preparado para dos tipos de ondas: Wave 1 y Wave 2. La primera hace que el robot ande en modo trípode, es decir, alternando un triángulo de patas, de manera que siempre hay tres patas en el suelo. El segundo modo alterna los movimientos de las patas de manera que siempre estén 5 patas en el suelo.

Adicionalmente se puede hacer que el robot sea o no sensible a obstáculos en el suelo, marcando o no el checkbox “Obstacles”. En caso de marcarlo, el robot podrá detectar terreno abrupto, como por ejemplo piedras y caminar sobre ellas manteniendo el cuerpo horizontal al suelo.

Diseño de la aplicación

La aplicación se ha generado en Visual C++ 6.0. Utiliza una librería desarrolladas por P.J. Naughter para el control del puerto serie con el que se comunicará con el robot.

Para más información sobre el manejo de la mencionada librería puede consultarse el trabajo del autor existente en la dirección:
http://www.codeproject.com/system/cserialport.asp

Adicionalmente utiliza una librería para el control del interface paralelo-I

2
C

Para más información sobre el manejo de esta librería puede consultarse el trabajo del autor existente en la dirección:
http://mundobot.com/tecnica/ki2c/spki2c.htm

El interface con el usuario consiste básicamente en un cuadro de diálogo asociado a una clase CMelanieDlg dentro de la cual se encuentran todas las funciones y variables utilizadas para el control del robot.

Los ficheros fuente de la aplicación contienen numerosos comentarios explicativos y pueden ser accedidos en la dirección:
http://mundobot.com/projects/melanie/v2/melanie2prg.zip

No obstante a continuación explicaremos la estructura general de la aplicación.

Grabación/Reproducción de
secuencias

Como se explicó anteriormente, es posible almacenar secuencias de movimientos. Para llevar a cabo esto se utilizarán punteros a estructuras almacenadas en memoria dinámica.

struct stPosition
{
unsigned char | cServoPos[21],
| cPause;
struct stPosition | *nextpos,
| *prevpos;
};

En cada elemento de esta estructura podemos almacenar una postura completa, que comprende la posición de 20 servos y el delay que deberá haber entre la postura anterior y esta. Adicionalmente se almacenan punteros a los elementos anteriores y posteriores para tener una lista enlazada en la que nos podamos mover libremente hace delante y detrás.

El almacenamiento en dicha estructura se realiza al pulsar el botón “Save Position” que llama a la función “OnSavepos()”. Dicha función toma los valores de posición de servos existentes en el cuadro de diálogo y los almacena en la estructura.

Si se está haciendo programación gestual, antes de pulsar el botón “Save Position” habrá que pulsar el botón “Check Position” que llamará a la función “OnAD()” y esta a “ChkPos(unsigned char
cPos[20],unsigned char cAD[20])” que toma los
valores de posición de los servos a base de leer el valor analógico de posición de sus potenciómetros internos. Este valor es convertido al valor de tamaño byte que enviado con el comando de posicionamiento de la tarjeta de control de servos colocaría los servos en la misma posición en la que están. Para conseguir esto el programa posee una tabla (byte bCal[21][4]) que almacena para cada servo dos valores para dos puntos de posicionamiento de los servos. Uno de los valores es el que enviado a la tarjeta de control de servos para que posicione el servo y el otro valor es la medición analógica tomada en dicha posición. Teniendo esto para dos posiciones de un servo se pueden obtener los valores de todos los puntos intermedios. Veamos esto con un ejemplo:

Para el servo número 1 se posicionó con los controles deslizantes en el valor 20 (el mostrado en el cuadro de diálogo) y se tomó el valor del potenciómetro (conversión A/D). El valor obtenido fue 59. La misma operación se realizó colocando el servo en la posición 198 obteniendo el valor A/D 195. Puesto que hay una relación lineal entre un valor de posicionamiento y la


una recta se puede calcular, en función de un valor A/D dado, cual es el valor de posicionamiento del servo. Así, si por ejemplo se lee el valor A/D del servo (voltaje en la patilla central del potenciómetro del servo) y dicho valor es, digamos 90, tendremos que el valor de posicionamiento del servo se obtendrá de la

Posicion = eje X

medida A/D tomada, utilizando la ecuación de

siguiente forma:

D = eje Y

e la recta = (20,59) y (198,195)

8)

8) = (59-195)/(20-198)*(x-198)

o los valores de A y B
mpíricamente para todos los servos y se cargan

a puede ser
olcada a fichero mediante la función

secuencias que estén
argadas en memoria, por lo que los botones de

o de la secuencia se lleva cabo mediante la utilización de la función

A

dos puntos d

x-b = m(y-a) {ecuación cartesiana de una recta}

Usando los puntos: (x=20 , y=59, a=198, b=195)

59-195= m(20 - 198)

m = (59-195)/(20 - 19

entonces :

y-195 = m(x - 19

AD-195 = (59-195)/(20-198)*(POS-198)

POS = 198+(AD-195)/((59-195)/(20-198))

Para AD=90, POS=60,6

Se han tomado por tant
e
en la matriz bCal por programa. Si se cambiasen los servos habría que calibrarlos de nuevo y actualizar los valores de esta matriz.

La secuencia existente en memori
v
“OnSaveseq()”. De igual manera cargarse un fichero en memoria mediante la función “LoadSequence(CString FileName)” que es llamada desde otras varias.

Solo se pueden reproducir
c
secuencias pregrabadas simplemente llamarán a funciones que carguen en memoria una secuencia pregrabada y la ejecute.

La ejecución de cada pas
a
“SetGlobalPos()”, que moverá los servos y controles deslizantes según los valores del puntero actual.

El delay (Pause) como se ha dicho, indicará el tiempo que debe transcurrir entre una postura y otro. Para que no existan momentos muertos, la
función | “cSpeed(unsigned | char | cServo)”
calculará la velocidad que se ha de aplicar a cada servo dependiendo de la pausa mencionada y del recorrido a llevar a cabo. Para ello se basa en especificaciones del fabricante de la tarjeta de control de servos que indica que el parámetro de velocidad ha de ser un valor entero entre 1 y 255 que se puede calcular según la siguiente fórmula:
| T
Pos Pos V 8( | 1− | 0) =

onde T es el tiempo en centésimas de segundo

l envío de comandos a la tarjeta de control de

unque la tarjeta de control de servos admite gran

SO: Activa todos los servos

ites de duty cycle

- para el
- vo “ss” (valor

ara más información sobre los comandos

2/msc2-cmd.htm

d
que se desea que tarde el servo en ir de una posición a otra, siendo Pos1 la posición de valor mayor y Pos0 la posición de menor valor. Los valores de Pos1 y Pos0 según especificaciones del fabricante de la tarjeta de control de servos han de ser valores enteros entre 0 y 250.

E
servos se realiza fundamentalmente mediante la función “SendCommand(CString sCommand)”.

A
cantidad de comandos, nosotros utilizaremos solo los siguientes:
- SF: Apaga todos los servos
- SX1F9D: Establece los lím
de los servos entre 496µsg y 2512µsg
SEss: activa la generación de pulsos
servo “ss”, valor que ha de estar en hexadecimal 00 - 13h (19d).
Mssddvv: Mueve el ser
hexadecimal) a la posición de 8 bits “dd” (valor hexadecimal entre 00 y FAh [250d]) a la velocidad “vv” (valor hexadecimal entre 1 y FFh [255d])

P
disponibles y su utilización, acceder a la documentación del fabricante: http://www.oricomtech.com/sub

Movimiento por desplazamiento de ondas

Como se ha comentado anteriormente, el robot puede desplazarse generando él mismo las posiciones en lugar de utilizar posiciones pregrabadas. El modo en que realiza esto es mediante la utilización de tres ondas cuyos valores variarán en el tiempo y definirán los valores de coordenadas (x, y, z) en el espacio del extremo de cada pata.


Teniendo estos valores, se utilizará un algoritmo geométrico de cinemática inversa y se obtendrá el valor de posicionamiento de cada servo para que el extremo de la pata se coloque en las coordenadas indicadas.

Cinemática Inversa

El programa hace los cálculos cinemáticos inversos que sean necesarios mediante la función

Int InvKinematic(double value[2][3], double result[3])

Esta función devuelve 0 si no ha ocurrido ningún error en el cálculo (por ejemplo podría darse que la coordenada dada esté fuera del espacio alcanzable por la pata).

Los datos de entrada
de la función se
cargarán en la matriz
value[2][3] de manera
que la primera fila de
datos contendrá las


longitudes en milímetros de las tres partes de la pata (L1, L2, L3) y la segunda fila contendrá las coordenadas (x, y, z) que se desea que tenga el extremo de la pata respecto de su origen de referencia. Como resultado la función cargará en la matriz result[3] los valores en grados de los ángulos que han de tener las articulaciones (a1, a2, a3)

El algoritmo utilizado para el cálculo de la cinemática inversa es de tipo geométrico.

Posteriormente pueden convertirse los valores de ángulos en grados de cada servo a valores de posicionamiento aceptados por la tarjeta de control de servos mediante el uso de la función
unsigned char cConvDegToPos(char cServo, double Deg),
donde cServo es el número del servo al que nos referimos y Deg es el valor en grados que deseamos que tenga dicha articulación. El valor devuelto por la función es el valor a enviar a la tarjeta de control de servos.

Para conseguir esto se utilizan valores de calibración para cada servo que han sido tomados empíricamente y son cargados al principio del programa en la matriz cPosConv[20][2].

El primer índice indica el servo y el segundo índice indica una posición de 0 grados y una de 45 grados. Por ejemplo, para la pata 1 se cargan los siguientes valores:

cPosConv[ 1][0]=203; | cPosConv[ 1][1]=140;
cPosConv[ 2][0]= 77; | cPosConv[ 2][1]=136;
cPosConv[ 3][0]=103; | cPosConv[ 3][1]=160;

La primera fila comprende los valores para el servo 1. 203 es el valor que requiere la tarjeta de control de servos para posicionar el servo de manera que el ángulo de la articulación sea 0 grados y 140 es el valor que requiere la tarjeta de control de servos para posicionar el servo de manera que el ángulo de la articulación sea 45 grados.


Con estos valores y, dada la relación lineal entre valor de posicionamiento y ángulo en grados de la articulación, podemos obtener siempre el valor de posicionamiento del servo en función del valor del ángulo de la articulación simplemente utilizando la ecuación de una recta.

Existe una función inversa a esta llamada
double cConvPosToDeg(char cServo, unsigned char cPos)

Cinemática Directa

El programa también lleva a cabo en algunos casos cálculos cinemáticos directos. Para ello utiliza la función:

int FwdKinematic (double value[2][3], double result[3])

Esta función devuelve 0 si no ha ocurrido ningún error en el cálculo.

El algoritmo utilizado es también de tipo geométrico.

Los datos de entrada
de la función se
cargarán en la matriz
value[2][3] de manera
que la primera fila de
datos contendrá las


longitudes en milímetros de las tres partes de la pata (L1, L2, L3) y la segunda fila contendrá los ángulos en grados de las articulaciones (a1, a2, a3). Como resultado la función cargará en la matriz result[3] los valores de las coordenadas (x, y, z) que tendrá el extremo de la pata respecto de su origen de referencia.

Generación de ondas

Como se ha comentado, son tres ondas las que definen las coordenadas que ha de adoptar cada pata en cada momento.

La coordenada X es calculada mediante una onda triangular, la coordenada Y mediante una semionda y la coordenada Z mediante una onda sinusoidal completa. La frecuencia de la onda triangular ha de ser doble de las otras dos para que la pata se mueva coordinadamente.

Variando el desfase entre las ondas de las diferentes patas y la relación entre la longitud de la primera y segunda parte del ciclo de la onda se podrán obtener diferentes “gaits”.

La primera parte del ciclo corresponde al momento en que el extremo de la pata está tocando el suelo y desplazándose hacia atrás (cuerpo avanzando), mientras que la segunda parte del ciclo corresponde al elevamiento y desplazamiento en arco de la pata hacia delante (posicionamiento para un nuevo paso). Así por ejemplo en la figura anterior, la primera y segunda parte del ciclo son de la misma longitud (en el tiempo), es decir que tardará lo mismo en desplazar la pata hacia atrás que en posicionarla de nuevo adelante. Si utilizamos este tipo de ondas en todas las patas, pero damos un desfase de 180 grados a tres de las patas, obtendremos un “gait” del tipo trípode, según el cual el cuerpo siempre estará soportado por tres patas.

Si por ejemplo utilizamos ondas del tipo anterior, pero con la 2ª parte del ciclo de una longitud 1/5 de la de la 1ª parte tendremos que la pata se elevará y colocará adelante en un tiempo determinado, mientras que se desplazará hacia atrás durante un tiempo 5 veces superior.
Si combinamos esta situación con un desfase de 36º (180/5) entre las ondas de las diferentes patas obtendremos un “gait” según el cual siempre habrá 5 patas en el suelo y solo una en el aire, pero el cuerpo se estará moviendo con una velocidad continua hacia delante.


Esto no es casual. Si deseamos que el cuerpo se desplace a velocidad continua, siempre ha de haber un número suficiente de patas en contacto con el suelo desplazándose hacia atrás, no pudiendo estar ninguna parada. Si queremos que siempre haya 5 patas en contacto con el suelo, habrá que ir levantando las patas una a una, de manera que 5 patas habrán de tener tiempo de elevarse y colocarse delante de forma consecutiva en el tiempo que la sexta pata se desplaza hacia atrás. Es decir que el tiempo de elevación y desplazamiento en el aire hacia delante de una


pata habrá de ser 1/5 del tiempo que tarda en desplazarse la pata hacia atrás. Esto es precisamente la longitud en tiempo de la 2ª parte del ciclo. Por otra parte, como se desea que solo una pata esté en el aire en cada momento (5 patas en el suelo), las ondas de las patas habrán de estar desplazadas 1/5 de 180º, ya que 180º es el punto en que la onda pasa de la 1ª a la 2ª parte del ciclo.

Es importante en este punto resaltar que las ondas utilizadas son las indicadas al principio de este apartado, es decir triangular, semionda y onda sinusoidal completa y que la variación de la longitud en tiempo de la 1ª o 2ª parte del ciclo no es más que una especie de “estiramiento” del tiempo y por tanto los valores en grados para su obtención también se “estiran”. Véase a lo que nos referimos para el caso anterior de la onda sinusoidal (Cosenoidal) que genera el valor de la coordenada Z:

En el programa se encuentra la función void OnWaveFwd() que hará caminar hacia delante según el método de desplazamiento de ondas explicado.

Siguiendo el mismo método de desplazamiento de ondas se ha generado la función MoveLeg que mueve el extremo de una o varias patas de un punto en el espacio a otro, bien trazando una línea recta entre ambos puntos o realizando un
movimiento | arqueado | de | levantamiento,
desplazamiento y bajada.

Debe recordarse que las coordenadas manejadas para cada pata son siempre relativas al punto origen de coordenadas de cada pata, según se muestra en la siguiente figura:

Detección de obstáculos

El programa está preparado para la detección de obstáculos en el suelo y adaptar el “gait” para permitir al robot caminar sobre dichos obstáculos.

El modo en que se hace esto es midiendo el consumo de corriente de los servos en el momento de bajada de la pata para posar su extremo sobre el suelo.

La medición del consumo de corriente se hace mediante la función void ChkCurr() que envía los comandos necesarios para llevar a cabo la lectura de los conversores A/D por bus I²
C y carga en la
matriz Current[6] los valores de medición de corriente de los 6 servos que más fuerza han de hacer para soportar el cuerpo.


Si la medida de consumo supera un umbral dado, se detiene la pata, se obtiene su posición y se modifica temporalmente la longitud de la segunda parte del ciclo de las ondas de dicha pata y se genera un pequeño desfase para asegurar que se desplazan coordinadamente con el resto de patas. Los valores de fase y longitud de la segunda parte del ciclo de dicha pata vuelven a sus valores normales en el siguiente ciclo, no produciéndose ninguna disrupción en la continuidad de las ondas durante la transición.

## Bibliografía y enlaces de interés

Entomología Agrícola. Daniel G. Pesante Armstrong. Capítulo 7: http://www.uprm.edu/wciag/anscience/dpesante/4008/cap-7.PDF Puchobot. Robot Cuadrúpedo. Andrés Prieto Moreno: http://www.iearobotics.com/personal/andres/proyectos/pucho/pucho.html Cube Reloaded. Gusano robot. Juan González: http://www.iearobotics.com/personal/juan/doctorado/cube-reloaded/
Curso de cinemática directa e inversa (Univ.Guadalajara-Mexico):: http://proton.ucting.udg.mx/materias/robotica/r166/r78/r78.htm
Legs. General design considerations: http://www.frasco.demon.co.uk/rodney/mechan/design.htm The Walking Machines Catalogue: http://www.walking-machines.org/
Silo4. Robot cuadrúpedo desarrollado por el CSIC: http://www.iai.csic.es/users/silo4/
An introduction to robot kinematics: http://www.generalrobotics.org/ppp/Kinematics_final.ppt MSCC20. credit card-sized control computers for driving up to 20 R/C servos. Oricom Technologies: http://www.oricomtech.com/mscc20.htm
CSerialPort v1.03 - Serial Port Wrapper. PJ Naugter: http://www.codeproject.com/system/cserialport.asp

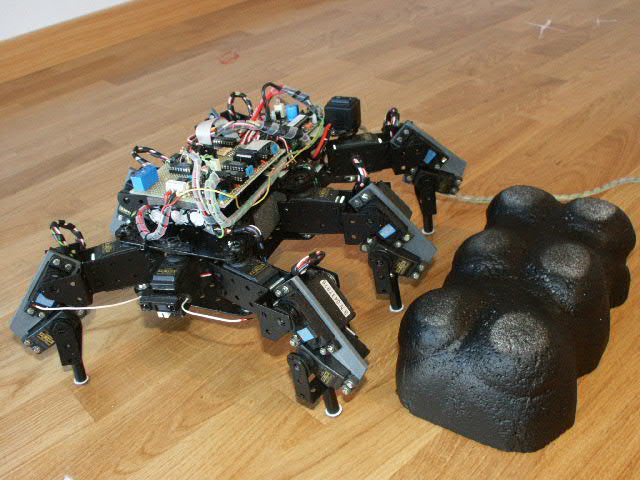
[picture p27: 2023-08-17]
Media/PICT0056.JPG

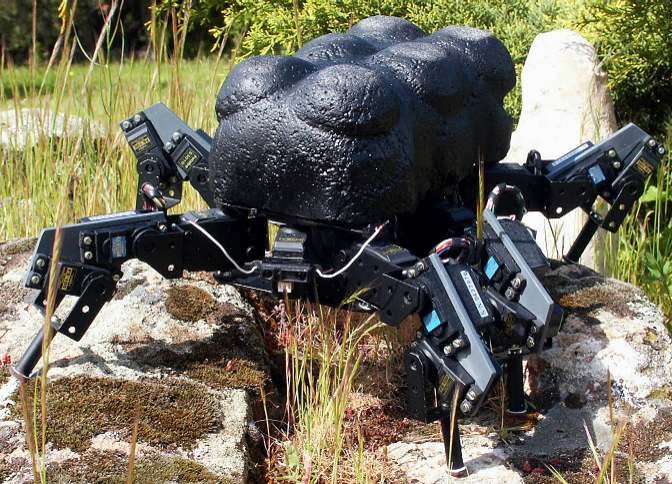
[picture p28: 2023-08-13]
Media/mel2c.jpg

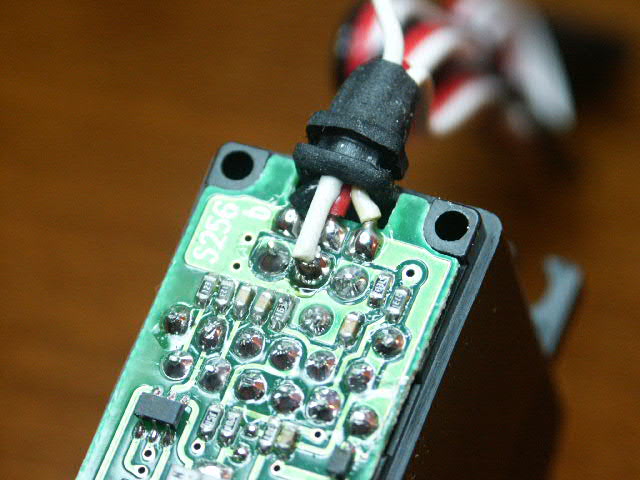
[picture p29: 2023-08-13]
Media/PICT0049.JPG

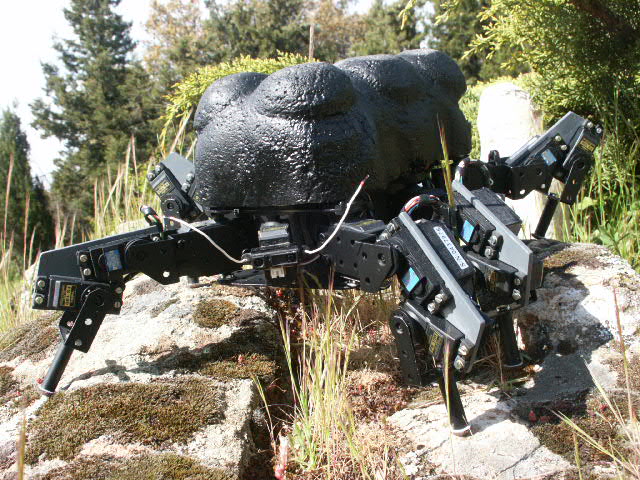
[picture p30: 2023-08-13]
Media/PICT0009.JPG

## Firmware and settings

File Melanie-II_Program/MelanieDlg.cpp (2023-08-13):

// Melanie v2.0
// by Alejandro Alonso Puig
// April 2004
// mundobot.com
//
// MelanieDlg.cpp : implementation file
//

#include "stdafx.h"
#include "Melanie.h"
#include "MelanieDlg.h"
#include <fstream.h>

#ifdef _DEBUG
#define new DEBUG_NEW
#undef THIS_FILE
static char THIS_FILE[] = __FILE__;
#endif


#define LEG1	0
#define LEG2	1
#define LEG3	2
#define LEG4	3
#define LEG5	4
#define LEG6	5

#define LEGS	6

#define LENGTH	0
#define ANGLE	1
#define COORD	1
#define X		0
#define Y		1
#define Z		2
#define COXA	0
#define FEMUR	1
#define TIBIA	2


#define PI	3.141592653589793238

/////////////////////////////////////////////////////////////////////////////
// CMelanieDlg dialog

CMelanieDlg::CMelanieDlg(CWnd* pParent /*=NULL*/)
	: CDialog(CMelanieDlg::IDD, pParent)
{

	//I2C addresses for the different modules
	cAD1Add		= 144;		//Address of the I2C A/D Converter 1
	cAD2Add		= 146;		//Address of the I2C A/D Converter 2
	cAD3Add		= 148;		//Address of the I2C A/D Converter 3
	cAD4Add		= 150;		//Address of the I2C A/D Converter 4
	cAD5Add		= 152;		//Address of the I2C A/D Converter 5
	cAD6Add		= 154;		//Address of the I2C A/D Converter 6
	cAD7Add		= 156;		//Address of the I2C A/D Converter 7
	cPORTAdd	=  64;		//I2C address Digital Ports module

	cPortVal	=0;			//Value of 8 bit digital port module

//Servo hexadecimal references as connected in MSCC20 module


	cServo[ 1]="0C";	// A2
	cServo[ 2]="06";	// B6
	cServo[ 3]="11";	// A4
	cServo[ 4]="0D";	// A5
	cServo[ 5]="04";	// B4
	cServo[ 6]="0B";	// C5
	cServo[ 7]="08";	// C0
	cServo[ 8]="02";	// B2
	cServo[ 9]="10";	// A3
	cServo[10]="12";	// C3
	cServo[11]="0F";	// A1
	cServo[12]="05";	// B5
	cServo[13]="0E";	// A0
	cServo[14]="00";	// B0
	cServo[15]="03";	// B3
	cServo[16]="0A";	// C2
	cServo[17]="09";	// C1
	cServo[18]="01";	// B1
	cServo[19]="07";	//B7
//	cServo[20]="13";

	//Values of position code for 0 and 45 degrees of each servo.
	//Used to make a relationship between degrees and position codes
	//sent to the servo control card.

	//Leg-1
	cPosConv[ 1][0]=203;	cPosConv[ 1][1]=140;
	cPosConv[ 2][0]= 77;	cPosConv[ 2][1]=136;
	cPosConv[ 3][0]=103;	cPosConv[ 3][1]=160;

	//Leg-2
	cPosConv[ 4][0]=195;	cPosConv[ 4][1]=139;
	cPosConv[ 5][0]= 85;	cPosConv[ 5][1]=143;
	cPosConv[ 6][0]= 85;	cPosConv[ 6][1]=143;

	//Leg-3
	cPosConv[ 7][0]=193;	cPosConv[ 7][1]=140;
	cPosConv[ 8][0]= 95;	cPosConv[ 8][1]=152;
	cPosConv[ 9][0]=118;	cPosConv[ 9][1]=178;

	//Leg-4
	cPosConv[11][0]= 25;	cPosConv[11][1]= 81;
	cPosConv[12][0]=168;	cPosConv[12][1]=109;
	cPosConv[13][0]= 80;	cPosConv[13][1]= 22;

	//Leg-5
	cPosConv[14][0]= 32;	cPosConv[14][1]= 91;
	cPosConv[15][0]=133;	cPosConv[15][1]= 73;
	cPosConv[16][0]= 95;	cPosConv[16][1]= 37;

	//Leg-6
	cPosConv[17][0]= 17;	cPosConv[17][1]= 79;
	cPosConv[18][0]=155;	cPosConv[18][1]= 99;
	cPosConv[19][0]= 77;	cPosConv[19][1]= 20;

	//{{AFX_DATA_INIT(CMelanieDlg)
	m_SliderServo01 = 0;
	m_SliderServo02 = 0;
	m_SliderServo03 = 0;
	m_SliderServo04 = 0;
	m_SliderServo05 = 0;
	m_SliderServo06 = 0;
	m_SliderServo07 = 0;
	m_SliderServo08 = 0;
	m_SliderServo09 = 0;
	m_SliderServo10 = 0;
	m_SliderServo11 = 0;
	m_SliderServo12 = 0;
	m_SliderServo13 = 0;
	m_SliderServo14 = 0;
	m_SliderServo15 = 0;
	m_SliderServo16 = 0;
	m_SliderServo17 = 0;
	m_SliderServo18 = 0;
	m_SliderServo19 = 0;
	m_ad01 = 0;
	m_ad02 = 0;
	m_ad03 = 0;
	m_ad04 = 0;
	m_ad05 = 0;
	m_ad06 = 0;
	m_ad07 = 0;
	m_ad08 = 0;
	m_ad09 = 0;
	m_ad11 = 0;
	m_ad12 = 0;
	m_ad13 = 0;
	m_ad14 = 0;
	m_ad15 = 0;
	m_ad16 = 0;
	m_ad17 = 0;
	m_ad18 = 0;
	m_ad19 = 0;
	m_pos01 = 0;
	m_pos02 = 0;
	m_pos03 = 0;
	m_pos04 = 0;
	m_pos05 = 0;
	m_pos06 = 0;
	m_pos07 = 0;
	m_pos08 = 0;
	m_pos09 = 0;
	m_pos10 = 0;
	m_pos11 = 0;
	m_pos12 = 0;
	m_pos13 = 0;
	m_pos14 = 0;
	m_pos15 = 0;
	m_pos16 = 0;
	m_pos17 = 0;
	m_pos18 = 0;
	m_pos19 = 0;
	m_pause = 80;
	m_seqname = _T("seqfile.txt");
	m_switch = FALSE;
	m_servo1 = FALSE;
	m_servo10 = FALSE;
	m_servo11 = FALSE;
	m_servo12 = FALSE;
	m_servo13 = FALSE;
	m_servo14 = FALSE;
	m_servo15 = FALSE;
	m_servo16 = FALSE;
	m_servo17 = FALSE;
	m_servo18 = FALSE;
	m_servo19 = FALSE;
	m_servo2 = FALSE;
	m_servo3 = FALSE;
	m_servo4 = FALSE;
	m_servo5 = FALSE;
	m_servo6 = FALSE;
	m_servo7 = FALSE;
	m_servo8 = FALSE;
	m_servo9 = FALSE;
	m_curr02 = 0;
	m_curr05 = 0;
	m_curr08 = 0;
	m_curr12 = 0;
	m_curr15 = 0;
	m_curr18 = 0;
	m_wave1 = TRUE;
	m_wave2 = FALSE;
	m_ObstaclesChk = TRUE;
	m_voltlog = 0;
	m_voltpow = 0;
	//}}AFX_DATA_INIT
	m_hIcon = AfxGetApp()->LoadIcon(IDR_MAINFRAME);

	//Initialize sequence of positions
	CreateSequence();

	//Open serial port
	port.Open(1, 9600, CSerialPort::NoParity, 8, CSerialPort::OneStopBit, CSerialPort::NoFlowControl);	

}

CMelanieDlg::~CMelanieDlg()
// Destructor
{
	delete(pstFirstPos);	//Free memory previously used
	port.Close();			//Close Serial Port

}
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

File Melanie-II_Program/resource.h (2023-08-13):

//{{NO_DEPENDENCIES}}
// Microsoft Developer Studio generated include file.
// Used by Melanie.rc
//
#define IDD_MELANIE_DIALOG              102
#define IDR_MAINFRAME                   128
#define IDC_AD03                        1000
#define IDC_AD                          1004
#define IDC_BUTTON1                     1006
#define IDC_CURRCHK                     1006
#define IDC_SLIDERSERVO01               1007
#define IDC_SLIDERSERVO02               1008
#define IDC_SLIDERSERVO03               1009
#define IDC_SLIDERSERVO04               1010
#define IDC_SLIDERSERVO05               1011
#define IDC_SLIDERSERVO06               1012
#define IDC_SLIDERSERVO07               1013
#define IDC_SLIDERSERVO08               1014
#define IDC_SLIDERSERVO09               1015
#define IDC_SLIDERSERVO11               1016
#define IDC_SLIDERSERVO12               1017
#define IDC_SLIDERSERVO13               1018
#define IDC_SLIDERSERVO14               1019
#define IDC_SLIDERSERVO15               1020
#define IDC_SLIDERSERVO16               1021
#define IDC_SLIDERSERVO17               1022
#define IDC_SLIDERSERVO18               1023
#define IDC_SLIDERSERVO19               1024
#define IDC_SLIDERSERVO10               1025
#define IDC_POS07                       1026
#define IDC_POS08                       1027
#define IDC_POS09                       1028
#define IDC_POS17                       1029
#define IDC_POS18                       1030
#define IDC_POS19                       1031
#define IDC_POS16                       1032
#define IDC_POS15                       1033
#define IDC_POS14                       1034
#define IDC_POS06                       1035
#define IDC_POS05                       1036
#define IDC_POS04                       1037
#define IDC_POS11                       1038
#define IDC_POS12                       1039
#define IDC_POS13                       1040
#define IDC_POS01                       1041
#define IDC_POS02                       1042
#define IDC_POS03                       1043
#define IDC_POS10                       1044
#define IDC_AD02                        1045
#define IDC_AD01                        1046
#define IDC_AD06                        1047
#define IDC_AD05                        1048
#define IDC_AD04                        1049
#define IDC_AD09                        1050
#define IDC_AD08                        1051
#define IDC_AD07                        1052
#define IDC_AD13                        1053
#define IDC_AD12                        1054
#define IDC_AD11                        1055
#define IDC_AD16                        1056
#define IDC_AD15                        1057
#define IDC_AD14                        1058
#define IDC_AD19                        1059
#define IDC_AD18                        1060
#define IDC_AD17                        1061
#define IDC_SAVESEQ                     1062
#define IDC_SAVEPOS                     1063
#define IDC_PAUSE                       1064
#define IDC_TOPBACK                     1065
#define IDC_ALLBACK                     1066
#define IDC_STEPBACK                    1067
#define IDC_STEPFORWARD                 1068
#define IDC_ALLFORWARD                  1069
#define IDC_TOPFORWARD                  1070
#define IDC_CLEARSEQ                    1071
#define IDC_LOADSEQ                     1072
#define IDC_LOADOVERSEQ                 1073
#define IDC_SAVEINVSEQ                  1074
#define IDC_SEQNAME                     1075
#define IDC_PRESET1                     1076
#define IDC_SWITCH                      1077
#define IDC_CURR02                      1078
#define IDC_SERVO1                      1079
#define IDC_SERVO2                      1080
#define IDC_PRESET2                     1081
#define IDC_PRESET3                     1082
#define IDC_PRESET4                     1083
#define IDC_WAVE_UP                     1084
#define IDC_PRESET6                     1085
#define IDC_PRESET7                     1086
#define IDC_PRESET8                     1087
#define IDC_PRESET9                     1088
#define IDC_PRESET10                    1089
#define IDC_PRESET11                    1090
#define IDC_PRESET12                    1091
#define IDC_PRESET13                    1092
#define IDC_PRESETSET1                  1093
#define IDC_PRESETSET2                  1094
#define IDC_WAVE_DOWN                   1095
#define IDC_VoltPow                     1096
#define IDC_SERVO3                      1097
#define IDC_CURR01                      1098
#define IDC_SERVO4                      1099
#define IDC_SERVO5                      1100
#define IDC_SERVO6                      1101
#define IDC_SERVO7                      1102
#define IDC_SERVO8                      1103
#define IDC_SERVO9                      1104
#define IDC_SERVO10                     1105
#define IDC_SERVO11                     1106
#define IDC_SERVO12                     1107
#define IDC_SERVO13                     1108
#define IDC_SERVO14                     1109
#define IDC_SERVO15                     1110
#define IDC_SERVO16                     1111
#define IDC_SERVO17                     1112
#define IDC_SERVO18                     1113
#define IDC_SERVO19                     1114
#define IDC_CURR06                      1115
#define IDC_CURR05                      1116
#define IDC_CURR04                      1117
#define IDC_CURR09                      1118
#define IDC_CURR08                      1119
#define IDC_CURR07                      1120
#define IDC_WAVE_PRESET                 1121
#define IDC_CURR12                      1122
#define IDC_CURR11                      1123
#define IDC_CURR16                      1124
#define IDC_CURR15                      1125
#define IDC_CURR14                      1126
#define IDC_CURR19                      1127
#define IDC_CURR18                      1128
#define IDC_CURR17                      1129
#define IDC_VoltLog                     1133
#define IDC_ALLON                       1134
#define IDC_ALLOFF                      1142
#define IDC_Wave1                       1143
#define IDC_Wave2                       1144
#define IDC_WAVE_FWD                    1145
#define IDC_OBSTACLESCHK                1146
#define IDC_BATTSTATUS                  1147
#define IDC_WAVE_FWDSHORT               1148

// Next default values for new objects
// 
#ifdef APSTUDIO_INVOKED
#ifndef APSTUDIO_READONLY_SYMBOLS
#define _APS_NEXT_RESOURCE_VALUE        130
#define _APS_NEXT_COMMAND_VALUE         32771
#define _APS_NEXT_CONTROL_VALUE         1146
#define _APS_NEXT_SYMED_VALUE           101
#endif
#endif
